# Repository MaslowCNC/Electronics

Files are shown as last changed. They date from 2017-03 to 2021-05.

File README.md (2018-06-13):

# Maslow Electronics

The printed circuit board which powers the Maslow CNC Machine

======================

Layout

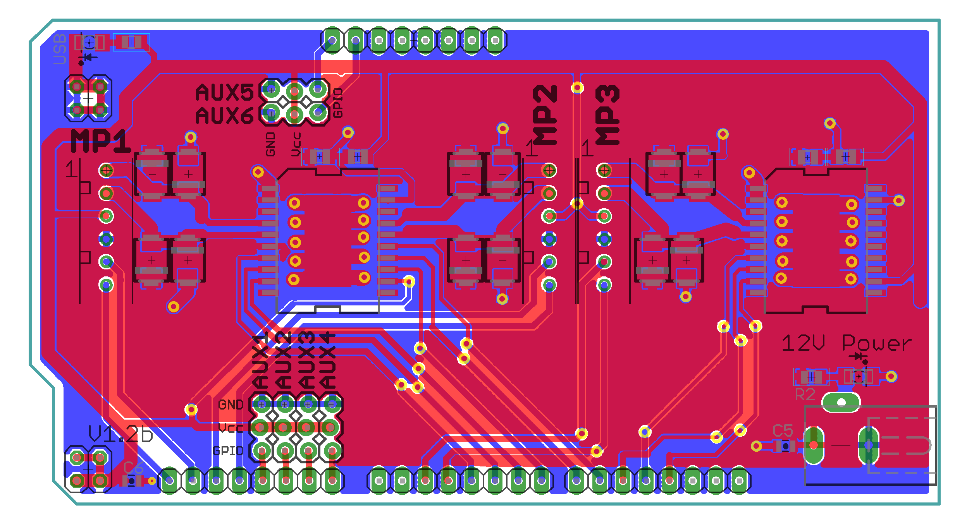
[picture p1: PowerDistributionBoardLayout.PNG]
Layout


Schematic

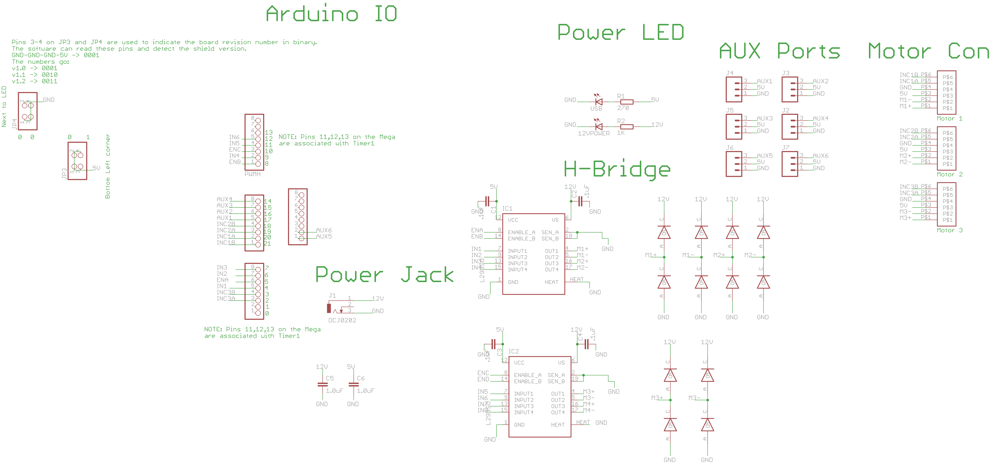
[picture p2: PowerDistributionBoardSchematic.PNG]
Schematic


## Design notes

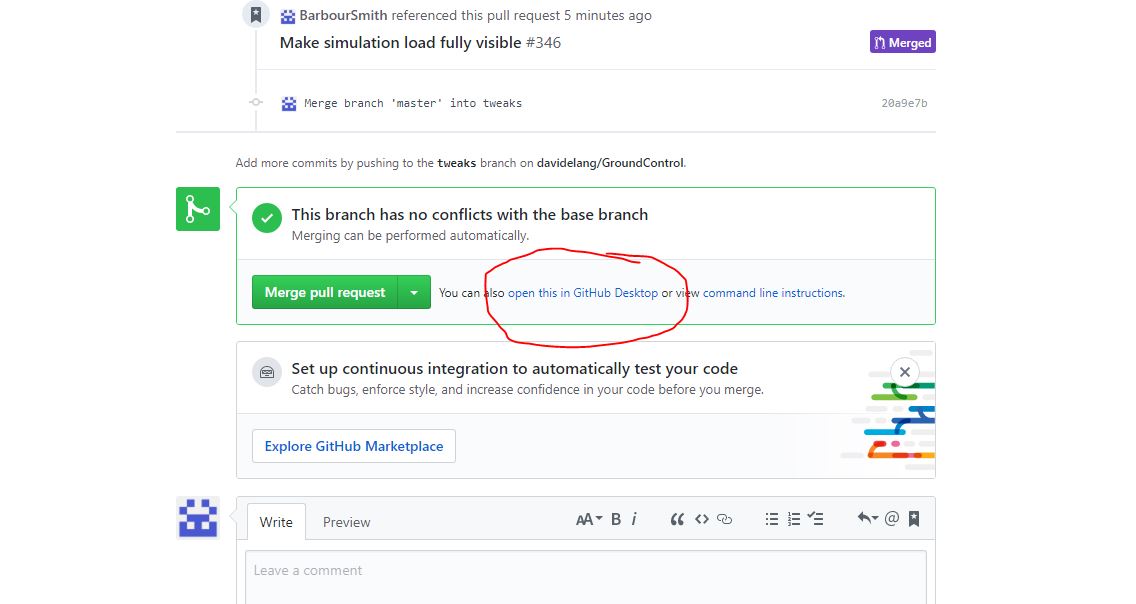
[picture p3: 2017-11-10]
Open This In GitHub Desktop.JPG

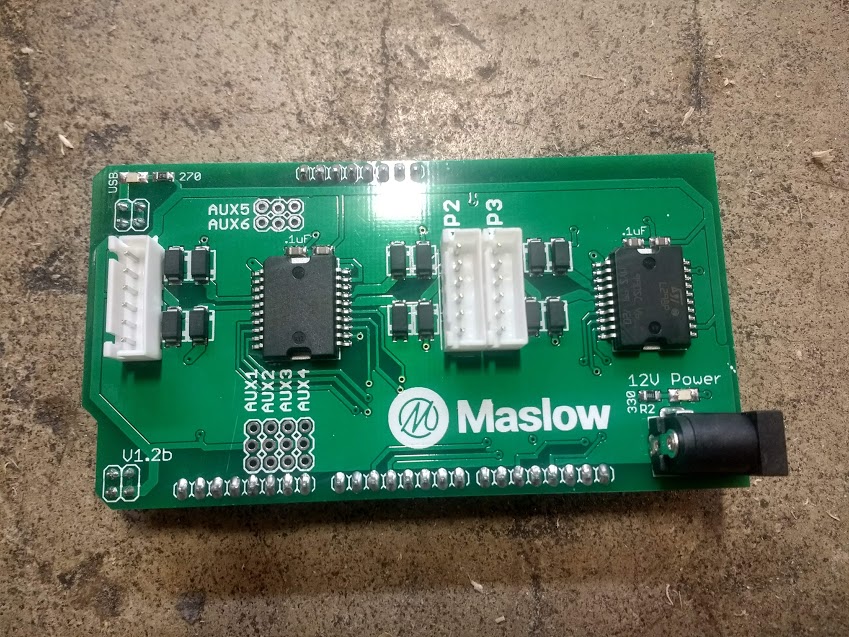
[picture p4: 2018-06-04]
mainpicture.jpg

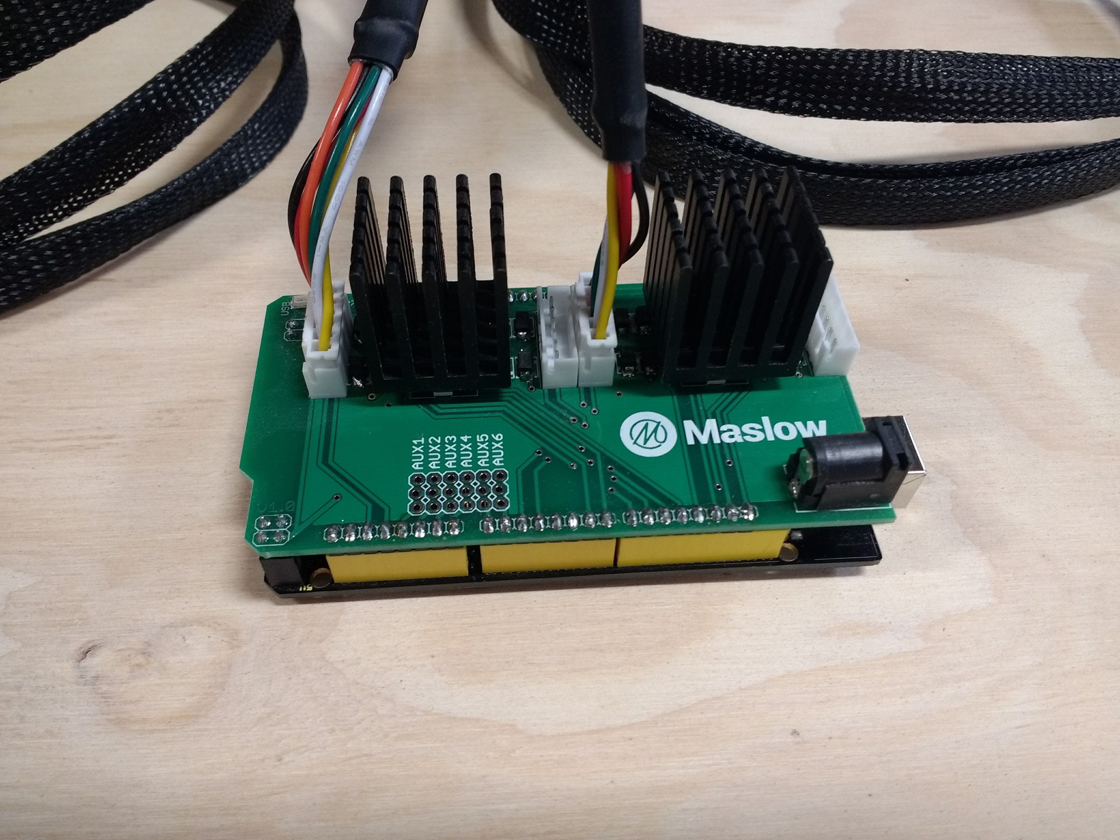
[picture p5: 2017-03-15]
Documentation/Motors Closeup.jpg

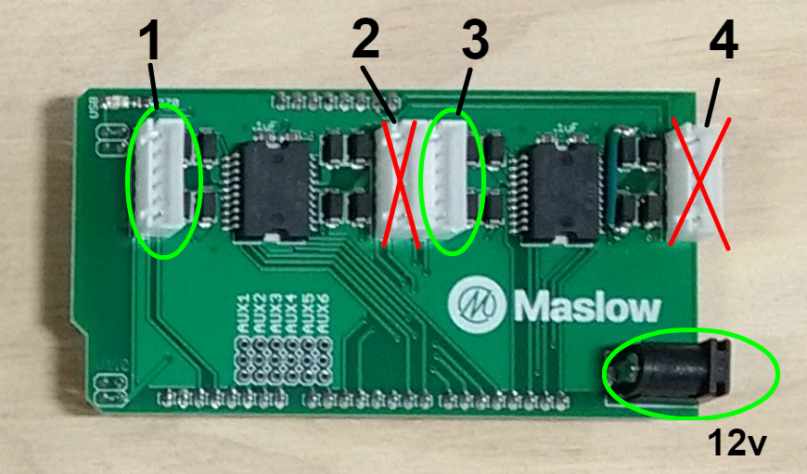
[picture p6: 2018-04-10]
Documentation/Port Closeup.png

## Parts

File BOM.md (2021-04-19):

# PCB BOM

All of the part numbers below are digikey parts unless otherwise stated.

| Part | Part # | Number Needed  | # In Schematic |
| --- |:---:|:---:|:---|
|XH-Series Connectors| 455-2271-ND | 3 | J1-3 |
| Power Jack | CP-202BH-ND | 1 | J4 |
| 1x8 .1" headers | 732-5321-ND | 4 | J5-8 |
| 2x2 .1" headers | 952-2119-ND | 2 | J9,10 |
| Flyback Diodes |  MRA4004T3GOSCT-ND  | 12 | D1-12 |
| .1uF Filter Caps | 311-1361-1-ND | 4 | C1-4 |
|  1uF Filter Caps | 445-5146-1-ND | 2 | C5,6 |
| H-Bridge | 497-3624-1-ND | 2 | IC-1,2 |
| Indicator LED | 475-1410-1-ND | 2 | LED 1-2 |
|Current Limiting R1 | RMCF0805JT270RCT-ND | 1 | R1 |
|Current Limiting R2 | 541-4162-1-ND | 1 | R2 |
| 23x23mm heatsink |Mouser-532-374124B35G| 2 | N/A |

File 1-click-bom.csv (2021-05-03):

References | Qty | Description | DigiKey | Mouser
J1-3 | 3 | XH-Series Connectors | 455-2271-ND
J4 | 1 | Power Jack | CP-202BH-ND
J5-8 | 4 | 1x8 .1" headers | 732-5321-ND
J9,10 | 2 | 2x2 .1" headers | 952-2119-ND
D1-12 | 12 | Flyback Diodes | MRA4004T3GOSCT-N
C1-4 | 4 | .1uF Filter Caps | 311-1361-1-ND
C5,6 | 2 | 1uF Filter Caps | 445-5146-1-ND
IC-1,2 | 2 | H-Bridge | 497-3624-1-ND
LED 1-2 | 2 | Indicator LED | 475-1410-1-ND
R1 | 1 | Current Limiting R1 | RMCF0805JT270RCT-ND
R2 | 1 | Current Limiting R2 | 541-4162-1-ND
N/A | 2 | 23x23mm heatsink |  | Mouser-532-374124B35G

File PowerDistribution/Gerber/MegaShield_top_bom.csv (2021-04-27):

Comment | Designator | Footprint | LCSC Part #
.1uF | 12VPOWER USB C1 C2 C3 C4 | C0805
1.0uF | C5 C6 | 0805-CAP
1K | R2 | R0805
270 | R1 | R0805
L298SO | IC1 IC2 | POWERSO-20
MRA4004 | U$2 U$3 U$4 U$5 U$6 U$7 U$8 U$9 U$10 U$11 U$13 U$14 | SMA

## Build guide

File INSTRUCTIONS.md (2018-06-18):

# Maslow Electronics Setup

We've done our best to keep the electronics for Maslow as simple as possible.

### Step 1: Identifying Parts
There are five pieces to the Maslow electronics system. Shown in the picture below from left to right and top to bottom they are:
1. The Motor/Encoder/Gear Box Units
2. Motor Wires
3. Maslow CNC motor controller shield
4. Keystudio Mega 2560 microcontroller (Arduino compatible) with USB Cable
5. 12V DC 5A / 110-250V AC Power Supply
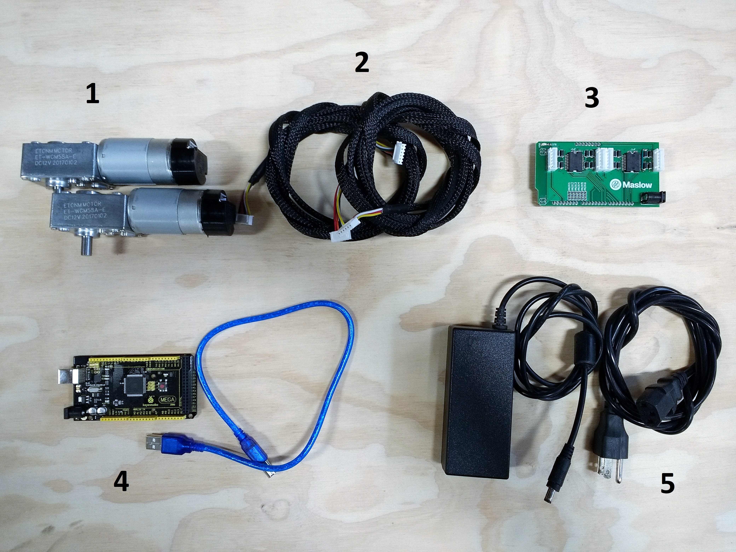
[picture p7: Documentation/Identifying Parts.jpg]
Identifying Parts


### Step 2: Attach Heatsinks
Attach the sticky backed heat sinks found in your hardware bag to the motor controller shield. (Note orientation of heatsinks)
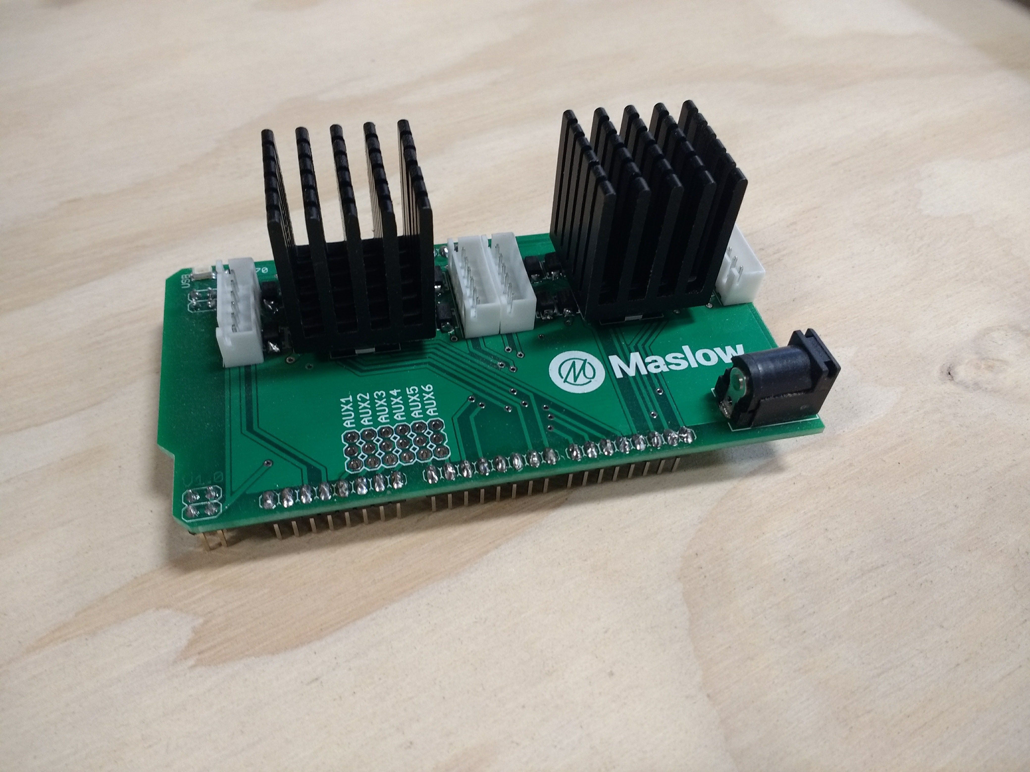
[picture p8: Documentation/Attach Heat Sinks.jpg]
Attach Heatsinks


### Step 3: Connect Arduino Shield
Attach the Arduino shield onto the Keystudio Mega 2560 microcontroller. Make sure all the pins are not twisted and that are aligned with the microcontroller before pushing the motor controller shield.
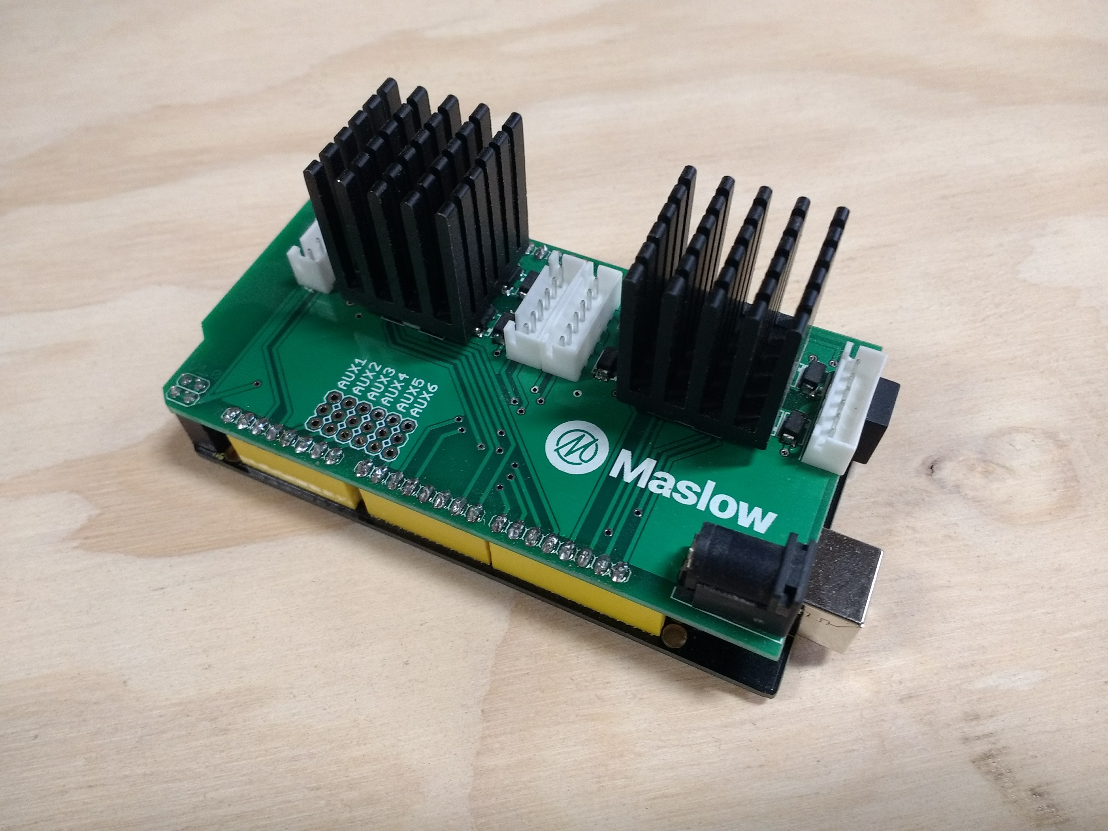
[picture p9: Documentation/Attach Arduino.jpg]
Attach Arduino


### Step 4: Connect The Motors
Attach the motors to the motor controller shield. **Note that the motors connect to ports 1 and 3 not 1 and 2**. This is to better distribute the motor power draw across both motor driver chips.  Port 3 controls the left motor and Port 1 the right motor (as viewed when facing the MaslowCNC).
The cables have two sides, so make sure that when plugged in the Arduino shield, the yellow wire is at the bottom in both ports as seen in the following photo.
When using the optional Z axis, this motor is connected to port 2.

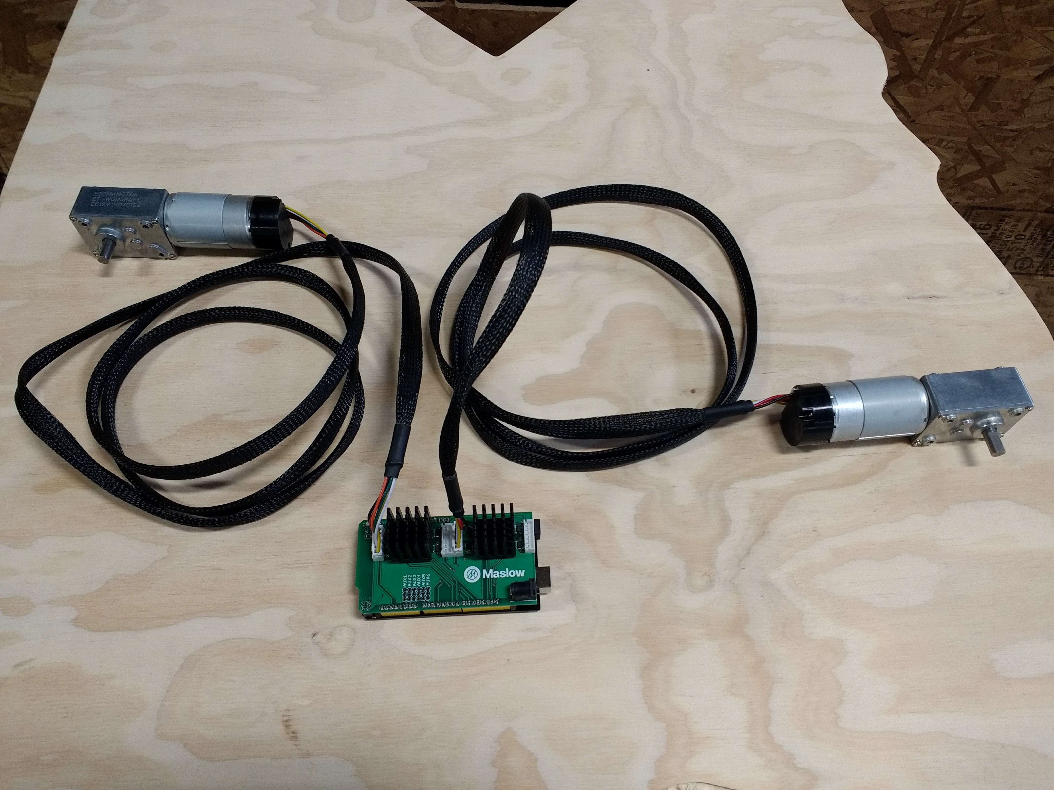
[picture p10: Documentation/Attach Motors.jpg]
Attach Motors


### Step 5: Connect The Power Supply
Plug the 12V power supply into the motor controller shield. **Note that the power supply plugs into the motor controller shield and not to the microcontroller.** Plugging the power supply into the Arduino will not damage it, but it also will not provide power to the motors. We chose the most common power supply plug to make replacements easy to find, unfortunately because it is so common this is also the same power supply plug that the Arduino uses, which is somewhat confusing.
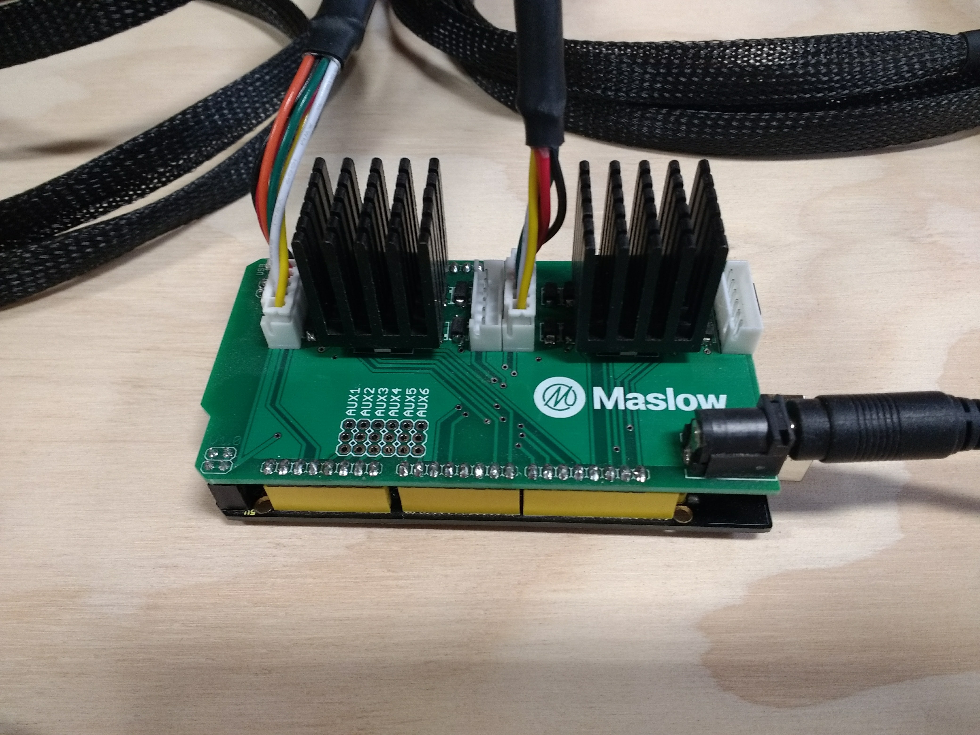
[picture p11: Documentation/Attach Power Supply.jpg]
Attach Power Supply


### Step 6: Connect The USB Cord
Plug the USB cord into the Arduino and into your computer. Note that the "USB" light will come on to indicate that the board is connected and receiving power from your computer.
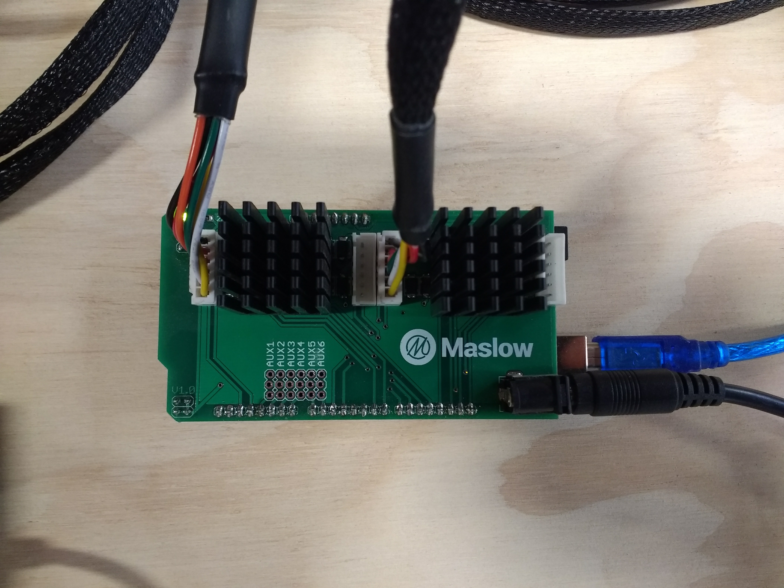
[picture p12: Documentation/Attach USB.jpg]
Attach USB


### Step 7: Proceed
You have finished setting up the Maslow electronics system. Proceed to the [next step](http://maslowcommunitygarden.org/Firmware.html?instructions=true) and install the open source Maslow Firmware on your Arduino.

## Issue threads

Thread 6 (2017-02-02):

BOM shows wrong HBridge

framecad-johnb, 2017-02-02:
The BOM currently shows a Digikey 497-1395-5-ND but the eagle file shows a surface mount component instead - I'm guessing it should be the Digikey 497-3624-1-ND, please confirm

BarbourSmith, 2017-02-03:
Thanks for catching that. I forgot to merge a pull request that fixed that. It should be up to date now.

Closed 2017-02-03.

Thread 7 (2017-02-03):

Check for continuity on 12V

blurfl, 2017-02-03:
In the area above and to the right of U$18 it looks like the top side copper pour (12V, I think) might be broken by the thru-hole of INCD1 and the keep-out around the ground pad of U$18. Is this the main 12V path to the rest of the board?
It might just be a difference in the way my tools are rendering the pours, though...
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

BarbourSmith, 2017-02-04:
That is definitely a real continuity issue. Thanks for catching that. Definitely the low point of my morning. I broke continuity there wiring up the 4th axis. I was in a huge rush to get those out because they are our longest lead time item. I am going to do a re-design next week and move all the components down so that top area is less cramped. For now I've added a wire to patch things in #8 just so the files up there aren't broken.

I checked in with the factory and its too late to do anything to the boards which are in production so I'll have to solder a wire to each of those which is pretty far from ideal. I guess this is why we do the whole beta thing.

A huge thank you again for catching that. That's a pretty big issue.

BarbourSmith, 2017-02-04:
I'd like to give you credit for having spotted the problem in next week's update. Is that OK? If so, do you have a way you would be preferred to be identified? (real name, blurfl, anonymous community member...etc)

blurfl, 2017-02-04:
I’d as soon not be identified, if that’s OK. Participation is important, glad I could help.

While I’ve got your ear, I’ve fished an old Arduino Mega 2650 out and put the firmware on it, but it seems pretty unhappy talking to GroundControl. Is it reasonable for me to try anything without the power board? Should I open a topic on the forum, or hold off until boards get to the betas?

Keep up the great work, you and Hannah are running an exciting project in an exemplary manner!

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

blurfl, 2017-02-04:
I’ve got stacks of boards with similar errors from previous projects.  A beta wouldn’t be proper without at least one “green wire”. :) The SMD Hbridges make good sense from a manufacturing angle, though. Worth the effort of the change.

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

BarbourSmith, 2017-02-04:
I'll order green wire to make the joke complete :-)

Thanks for the support. We do our best, but we really couldn't do it without you.

I wouldn't expect the lack of a power board to matter to the serial connection. What types of issues are you seeing? I tried to increase the baud rate last week and started running into issues and stepped it back so making sure you are using the current version might make a difference. I'm working on getting a Mac computer and a Raspberry Pi set up as two more test platforms in the next week. I was seeing some connection issues on the Mac which I haven't explored yet. What type of platform are you running GC on?

It might be worth filing a bug on GC for this or making a thread in the forums. I think it's something important to explore.

Closed 2017-02-05.

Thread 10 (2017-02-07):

Missing part on BOM?

pronettixs, 2017-02-07:
While reviewing the PCB in Eagle i noticed 2 component with i could not find on the BOM.
Above the H-Bridges there are 2 SMD components. Are these .1uF capasitors?

![Uploading missingParts.JPG…]()

pronettixs, 2017-02-07:
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

BarbourSmith, 2017-02-07:
Those are the .1uF filtering capacitors. I added the value to the description on the BOM to make it more clear. Thanks for pointing that out.

Do you think that's clear enough, or is there more we can do to make it clearer?

pronettixs, 2017-02-10:
Thanks, this is clear enough.

Closed 2017-02-10.

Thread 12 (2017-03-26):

Power LED should show 12V power instead of 5V

blurfl, 2017-03-26:
There presence of 5V power can be assumed if the USB connection is made; the presence of 12V power is necessary for the motors, and using this led for that would make it easy for a user to know he has the power supply correct. Relabel it '12V' or 'Motor Power'.

BarbourSmith, 2017-03-27:
Glad there is an issue for this, I agree 100%

blurfl, 2017-03-27:
It should be an easy edit, but if the boards have already been ordered…

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

BarbourSmith, 2017-03-27:
😬 It's hard to change things once the order goes out.

I've been putting off placing the next batch order to get as much feedback as possible rolled into them, but I think I need to ship them in the next few days. The basic design will be the same as in PR #9 with a 12v LED indicator added.

blurfl, 2017-03-27:
That should do it 👍

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

Closed 2017-04-11.

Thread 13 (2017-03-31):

Power supply connection

neilfrazerm, 2017-03-31:
Instructions  at setep for for those internationals without a power supply provided.
Please advise / insert the size of the connector and/or suggest supplying one in the kit if no power supply provided.
Thanks
Neil

BarbourSmith, 2017-04-01:
I checked in with Hannah and I realize this is totally my fault. I intended for those of you who live in countries with different power requirements to still receive the power supply, but just no power cord.

I chose a power supply which works from 100-250vac 50/60hz, and which uses a standard computer power cord so that they would be easy to find with the correct plug for your country.
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

I didn't make that clear enough and we ended up sending you no power supply at all. The power supply is on the way, but I understand if you don't want to wait for shipping time and want to buy one locally. I'm really sorry for the mix-up, it was completely my fault.

Fortunately, the other side of the power supply is also the most common connector I could find. Its a 5.5mm barrel connector with a 2.1mm pin. A 5.5mm barrel connector with a 2.5mm pin will also fit. The center pin is positive (standard). The supplied power-supply is a 5A  12V dc supply with self resetting fuses for over-current and over voltage protection, but almost any 12volt supply will work.

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

The power supply for the motors is isolated from the electronics so the quality of the voltage is not critical. Almost any 12 volt will work. I am more than happy to look at particular supplies if you want, and if you can find one locally that will ship more quickly than the original one which is in the mail, we are more than happy to pay for it and have it sent to you.

Again, I'm sorry for the mixup.

neilfrazerm, 2017-04-01:
Thanks awfully for sending out the supply, as you have already done so, and I am away for the next week, I shall wait for yours...

I had found the right connector from Maplins (UK Farnell equivalent) .

I do understand the pressure you are under and really do wish you rather well old chap.

Sincerest best regards,

Neil

(London)

________________________________
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

blurfl, 2018-01-10:
@BarbourSmith, this looks like it could be closed, but your reply and its pictures look like good wiki fodder 😀

Closed 2018-01-10.

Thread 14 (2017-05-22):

Motor Control Pins - are two GPIO pins necessary?

blurfl, 2017-05-22:
It looks like the two motor control pins are always used in complementary states in Motor.cpp. Could each motor be controlled by one GPIO and an inverter to use fewer GPIO pins?

BarbourSmith, 2017-05-23:
No, we could really use just one pin and an inverter.

Using two pins keeps the part count down (we've already got the pins).

In theory we could do active braking of the motor by using both pins high (or maybe it's low), but I haven't played with that option yet.

blurfl, 2017-05-23:
Using one pin eases the task of adapting other cpu options (ESP32). The inverters could live on the adapter board instead of on the motor board.
With the present gearing setup, would adaptive braking accomplish much?

Closed 2017-05-23.

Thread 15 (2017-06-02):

PWMH Connector

1996Donzi, 2017-06-02:
Per the eagle file the connector labeled PWMH has two pins (IN7 and IN8) if I am looking at the Arduino Mega  schematic properly they are tied to GND and AREF, is this correct?

BarbourSmith, 2017-06-02:
You are correct, that was a mistake. The latest PCB version (updated this morning) removes that connector.

Closed 2017-06-06.

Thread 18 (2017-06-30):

Missing Heatsink from BOM

JDogHerman, 2017-06-30:
In the pictures I see a heatsink shown but it is not an item on the electronics BOM. Can this be added?

BarbourSmith, 2017-06-30:
Great point! Yes it can

BarbourSmith, 2017-06-30:
I've added it to the BOM. Its good that it is in there to remind people to order one when buying parts. I can't give you a digikey number for the part because we had ours custom made, but it's not a critical part. Digikey sells a number in the right size range.

JDogHerman, 2017-06-30:
Will there be a method of purchasing these "one off custom" parts from the MaslowCNC org?

JDogHerman, 2017-06-30:
What sort of thermal resistance is required?

JDogHerman, 2017-06-30:
Would a part like Digikey: 345-1103-ND work? Its a "little" larger but it already has the adhesive base.

BarbourSmith, 2017-07-01:
That one looks perfect. I measured the space and it will fit. I would recommend the taller 25AB model because the short one might not move enough heat.

If you want to throw it in the BOM that would be fantastic.

We're probably never going to sell the heatsinks individually because it's not really cost effective, but we will probably sell the whole arduino shield as a board with the heat sinks in the next few weeks

JDogHerman, 2017-07-01:
Added the suggested heatsink to pull request #19

schlaubi0666, 2017-07-12:
the sugested one is also 6.4mm in heigth, but the one on the Picture is much taller ...
is this ok , to use the not so tall Version?
or better use ATS1319-ND ?

JDogHerman, 2017-07-12:
@schlaubi0666 It looks like the ATS1319-ND does not have numbers for thermal resistance while being naturally cooled.  Its also more than 3 times the price. (might be necessary) @BarbourSmith does this part @schlaubi0666 suggested look like a more fitting part?

JDogHerman, 2017-07-12:
The nice thing is since the H-Bridge is over-temped protected and it is a closed loop system, if the H-Bridge does go into over-temp the encoder will detect that it has missed steps and the cut wont be lost.

In a future board design it might be nice to use L298N as it has much better thermal transfer numbers vs the L298P. 3C/W vs 13C/W*while using a aluminum substrate (not used in current boards)

BarbourSmith, 2017-07-12:
While they say it's over temp protected, we've blown up enough at this point to put that in the false marketing category ☹️

I think I tracked down a part that I was looking at as a replacement in the future, but I can't remember what it is off the top of my head. Moving away from the L298 family is in the future.

blurfl, 2018-01-10:
@BarbourSmith, have you got a heatsink (and thermal tape) part number for the BOM?

Also your comment "Moving away from the L298 family is in the future." [Issue #23](https://github.com/MaslowCNC/Electronics/issues/23) is a discussion about this general topic - any further thoughts?

BarbourSmith, 2018-01-10:
We ended up having them custom made 🙄 so I don't have a part number. It's weird how it's cheaper to have a heatsink made to spec than to buy one off the shelf

I hadn't given too much thought to moving away from the L298 family because we stopped blowing them up with such regularity...I still think moving is a good idea...I am a little worried about possible effects to the PID tuning

blurfl, 2018-01-10:
I think I've ordered replacements for these.I think I've got Digikey part numbersfor the [thermal tape](https://www.digikey.com/product-detail/en/3m-tc/15MM-15MM-10-8810/3M10310-ND/2649855) and the heat sinks, but I haven't found the heat sink one yet 🙃. I'll keep looking and reply to this issue.

blurfl, 2018-01-10:
I was wrong, the heat sinks were for a different chip family, not applicable. Are there enough on hand to offer them in the Maslow store?

blurfl, 2018-01-12:
[This](https://www.mouser.com/productdetail/aavid-thermalloy/374124b00035g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) heatsink from Mouser is 23mm x 23mm and 18mm high, so slightly shorter but in the ballpark. In stock, $2.35 each, includes the thermal tape.

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

BarbourSmith, 2018-01-12:
That looks like a perfect solution!

blurfl, 2018-01-12:
Shall I add it to the BOM in the same PR that updates the schematic and silkscreen, or would you like them separated?

BarbourSmith, 2018-01-12:
Having a lot of pull requests that change the board files themselves can be tricky, but doing this as a separate PR should be safe I think

blurfl, 2018-01-12:
Oops, I'll pull the PR back and separate them - sorry, jumped the gun!

blurfl, 2018-01-12:
While I'm at it, should I be saving these files in a particular version of EAGLE v8.5 is current, but it offers an option to save for EAGLE v7.x ?
Also, I'd like to remove the backup files and lock file that EAGLE leaves around - only the .sch and .brd files in the repo.

blurfl, 2018-01-12:
@BarbourSmith, here's the situation - The pin label changes affect the schematic visibly and the board invisibly, so both must be changed together. The silkscreen change affects the board but not the schematic, but both files should still be submitted together.
 I did the schematic change first as it made a bigger change. Shall I remove the diode symbols from the board file that goes with the schematic change, open a PR for just the schematic change, then add the diode symbols to the silkscreen after the schematic PR is merged?

BarbourSmith, 2018-01-12:
Right, I see the issue

Is it possible to submit just both changes at once? I think that would be totally OK

blurfl, 2018-01-13:
This was addressed in PR#41 - is it Ok to close this?

BarbourSmith, 2018-01-13:
I vote to close this one as well. You are really knocking these off!

Closed 2018-01-13.

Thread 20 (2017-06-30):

Heatsink substrate

JDogHerman, 2017-06-30:
I might be wrong in this, but would it be good to add a thermal substrate copper pad for the H-Bridge ICs to sit upon?

BarbourSmith, 2017-07-01:
I think it's a great idea. We actually had one in an early version of the PCB, but I took it out because our PCBA people were having enough trouble and I wanted to make things really really really easy for them. It might be time to put that back in. The ground plane runs right under each chip to make doing exactly that easy.

JDogHerman, 2017-07-01:
Sorry I opened this and then looked closer at the traces and saw that the traces run underneath the ICs.

dmouw25, 2017-09-01:
Is it possible to Reopen this?   These packages are designed to dissipate most of the heat through slug on the bottom of the package.  If you notice, the datasheet does not give thermal values for junction to case.   You would likely get better thermal performance with a redesigned PCB and no heatsink.

JDogHerman, 2017-09-01:
Reopened as a feature request.

blurfl, 2018-01-10:
I believe this was addressed in the v1.2 layout. @JDogHerman, @dmouw25 does that look correct to you? If so, we could close this.

BarbourSmith, 2018-01-10:
I second that it was a great suggestion and has been added

Closed 2018-01-10.

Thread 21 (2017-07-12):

how to get a pcb

schlaubi666, 2017-07-12:
i missed Kickstarter, and you do not know it you are selling kits again ;-(

1. do you will provide an partlist soon ?

the most difficult part to get is the pcb of the Driver ....

2. you have some spare modules to sell ?

3. it not, can you provide the gerber data to order my own pcb ?
4. what is the spec/Parameter of your ordered pcb's ?

br

Dirk

BarbourSmith, 2017-07-12:
We're hoping to start selling individual parts really soon, so hopefully in a couple weeks you will be able to buy an arduino shield from us in the next few weeks.

Until then, we do have a parts list here: https://github.com/MaslowCNC/Electronics/blob/master/BOM.txt and the gerber files are available here: https://github.com/MaslowCNC/Electronics/tree/master/PowerDistribution if you want to make your own.

The specs for the boards are nothing special. Maybe 16mil trace width and 1oz copper. Anyone who can make PCBs should be able to make one for you.

JDogHerman, 2017-07-14:
@schlaubi0666 I am in the same boat with you. I put in an order for a PCB and got more than I needed (min quantity). PM me if you would like me to get you one at cost+shipping.

schlaubi0666, 2017-07-15:
the part list  a was taking about , is the whole list , not just the electronics ...

schlaubi0666, 2017-07-15:
@JDogHerman : i did not found an way th contact you (PM) , so yes i would like to have on. plz. write me an email to my username + @gmx.de

JDogHerman, 2017-07-17:
@schlaubi0666 I got an email bounceback from the gmx.de server. Is there another address I can contact you at?

ndefoor, 2017-07-18:
@JDogHerman Could you message me  nathandefoor@hotmail.com I would like to see about getting one of those extra boards. Thanks

mgood83, 2017-07-20:
@JDogHerman could you also message me in regards to purchasing a board from you. I was just about to get one made, but if you already have spare, even better. Happy to pay send payment for cost + time +shipping. Thanks. mwgoodlett@gmail.com

clintloggins, 2017-07-20:
@JDogHerman please count me in if you have another pcb. More than happy to pay a premium!! Also, any of the changes that you discussed I am willing to test and give feedback. Thanks!
clintloggins@gmail.com

schlaubi666, 2017-07-20:
thanks for selling the bord now in your shop , i will grab one there ....

ndefoor, 2017-07-26:
I am looking for the specifics on the motors.  Does it matter if the rpms are slightly different?

JDogHerman, 2017-07-26:
@ndefoor There is a discussion on alternative motors options on the forums.

[forum link](http://forums.maslowcnc.com/t/for-those-that-were-not-part-of-the-kickstarter-where-to-obtain-the-main-motor-worm-gear-encoder/120)

JDogHerman, 2017-07-26:
This issue can be closed.

Closed 2017-07-26.

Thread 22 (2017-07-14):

Silkscreen is missing LED polarity

JDogHerman, 2017-07-14:
It might be nice to see the LED polarity shown on the silkscreen for those of us that are sadistic enough to build our own boards.

Also why not show a website address? maslow.cnc 👍

BarbourSmith, 2017-07-17:
Those are both great suggestions

blurfl, 2018-01-10:
I'm going to be into the design files working on the schematic for [issue #36(https://github.com/MaslowCNC/Electronics/issues/36). I'll open a separate PR to add this and update the board .jpg as well.

blurfl, 2018-01-11:
Rather than draw an LED symbol, I've put a plus sign opposite the positive end of each of the two LEDs:
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

If that's satisfactory, I'll put in a PR with the change.

BarbourSmith, 2018-01-11:
I think that looks great!

BarbourSmith, 2018-01-11:
There is a small dot on the LED part, does that not indicate polarity?

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

BarbourSmith, 2018-01-11:
My read of the schematic is that the polarity should be like this:

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

blurfl, 2018-01-11:
Thanks Bar, you're right. Hard to turn my thinking around to 12V power plane and routed ground. The dot _does_ indicate polarity, but I think it wouldn't appear on the silkscreen of a PCB in a maker's hand because it's in a keep-out area. The plus would address that. You've got a good point, though - SMD LED's use a dot to mark the cathode end. How best to address the issue, dot-at-cathode or plus-at-anode? @JDogHerman, what's your opinion?

BarbourSmith, 2018-01-11:
I think the plus is a great idea! I was just pointing out the dot because I was curious what it meant. You are absolutely right that it does not show up anywhere on the PCB. I actually had an email from the manufacturer this morning to confirm the diode directions so even they are confused 😛

The plus will be much better.

blurfl, 2018-01-11:
Just to stir the pot, how about:
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

and
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

BarbourSmith, 2018-01-11:
SLICK! I love it

blurfl, 2018-01-13:
This was addressed in PR#42 - is it Ok to close this?

BarbourSmith, 2018-01-13:
Also beautifully taken care of. I vote to close.

Closed 2018-01-14.

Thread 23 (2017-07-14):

New board design discussion.

JDogHerman, 2017-07-14:
Since this shield has lots of room on it what if there was thru-hole passive components holes added to the board in addition to smb. That way the board could be built as a kit easier for mortals.

BarbourSmith, 2017-07-17:
It might seem like there is a lot of space, but a lot of the open copper is actually left intentionally open because we have a lot of current flowing across the board. I'm open to the idea if someone can design one that looks good, but I think we'd be better off doing a second board that's the through hole version if we want that

JDogHerman, 2017-07-17:
If the XH connector housing was moved down it would allow for more room for the A+ B+ motor lines to be widened and permit though hole diodes to be added. (in addition to reducing the trace length)

The current limiting resistor and LEDs have plenty of board room and the filter caps could be moved closer to the supply rather than near the H-Bridges. #27

In addition if the MP3 H-Bridge was moved to the right it would help provide less thermal coupling with the other H-Bridge.

BarbourSmith, 2017-07-17:
Those are great points! If you make those changes, I'd be more than happy to merge them. My only reservation is that I think I'm going to redesign with a new H-bridge chip so we're probably going to see a lot of changes soon

JDogHerman, 2017-07-17:
@BarbourSmith what H-bridge chip are you thinking? Maybe I can help propose a layout with the new chip in mind.

BarbourSmith, 2017-07-17:
That would be great! I'm thinking about using the L6206 (https://www.digikey.com/product-detail/en/stmicroelectronics/L6206PD013TR/497-3643-1-ND/677626)

JDogHerman, 2017-07-17:
Interesting. The L6206 has integrated diodes, and higher current capacities, but if thermal considerations havn't been built into the PCB. The heat will skyrocket with 62 C/W! 🔥

BarbourSmith, 2017-07-17:
Good spot, that's something we need to consider. 62C/W is nuts, how does anyone keep that cool?

JDogHerman, 2017-07-17:
Looks like you can get it down to 15C/W by having it

> Mounted on a multilayer FR4 PCB with a dissipating copper surface on the top side of 6 cm2 (with a thickness of 35 µm),
> 16 via holes and a ground layer.

then maybe adding heatsinks and active cooling could keep it cool. ❄️

Also did you see that digikey has limited numbers of this pn?

BarbourSmith, 2017-07-17:
I (clearly) didn't do too much research into finding a replacement part yet, and I'm rapidly becoming convinced that the L6206 is not the best choice. Are there any other candidates out there that look more promising?

JDogHerman, 2017-07-17:
What features are you hoping to achieve?
More current? Higher voltage? Better thermal characteristics? Faster switching?

BarbourSmith, 2017-07-17:
I'd say the #1 thing we need is durability. I'd like a chip that we can short without blowing it up, and which doesn't overheat easily. Other than that our needs are for a pretty basic 12v 2A+ H-Bridge

JDogHerman, 2017-07-18:
Have you seen this? [TLE5206-2GCT-ND](https://www.digikey.com/products/en?keywords=TLE5206-2GCT-ND)

Low Thermal Resistance, Internal Inductive Diodes, Short circuit protection with a error pin so software could alert the user that there was an issue. Cost is higher but isnt bad.

Better pcb thermal design features and a heat sink would still be necessary but the chip should have better reliability since it will have more headroom vs the existing [chip 497-3624-1-ND](https://www.digikey.com/product-detail/en/stmicroelectronics/L298P013TR/497-3624-1-ND/677613)

BarbourSmith, 2017-07-18:
Crikey, I love it! Excellent find! The price is pretty reasonable even with one needed per motor. The board will still be a couple $ more, but for full output short circuit protection it's absolutely worth it.

I'll see if I can throw together a board to test them this weekend, when I have PCBs made, I'd be more than happy to send you some to test too if you'd be interested.

blurfl, 2017-07-18:
I’d like to test or help with the design too, if I might.
When laying it out, here are some things to think about:

- Could we re-think which pins are used for board ID? The present approach interferes with the ICSP pins, making porting to other processors harder and making it harder to use SPI. Too, using a pull-up/down resistor adds parts count, but protects the gpio pins.
- As we don’t need the braking function, the new layout could use hardware inverters to handle the complement motor drive signals.
- It would be harder to deal with heat sinks, but putting the motor drivers on daughter boards or using the thru-hole version of these chips would make it easier for mortals to repair. Selling motor drive daughterboards as spares would mean less electronic waste when the drivers need replacement.

JDogHerman, 2017-07-18:
@BarbourSmith that sounds great. If you want help with ideas on the design of the PCB let me know. I would be thrilled to test or help design. Just let me know how I can help. We could even add this as a project to github.

@blurfl I too would think a new method for identifying board revisions might be nice.  In fact if there was interest in changing the H-Bridge communication path to SPI there are other chip that could fill that need.

blurfl, 2017-07-18:
Having SPI available would make it possible to add SD card support.

- gcode transfer serial buffering is an ongoing issue. With a local file system we could transfer separately from the cutting process and the read from there while cutting instead.
- This could make off-line operation possible as well.
- Finally, some other processor boards have higher speed, but don’t have the non-volatile storage of the Mega. An SD card would open up those possibilities as well.

 So, while I build my wish list, let me add at least the traces for a micro SD card :)

BarbourSmith, 2017-07-19:
Any and all help is more than welcome, if you want to have a go at putting together a board with the TLE206 or any other chip that you think is worth a go I would love to try it out!

I agree that adding an SPI interface could be nice. My general preference is to keep the whole machine as simple and low cost as possible to keep it reliable and affordable, but that doesn't mean we couldn't have the pins broken out to attach an SD card daughter board. Going to SPI for the motor controllers is also an option. I used the simplest most reliable interface for the boards so far because I wanted to focus on getting as simple and robust a system as possible built, but now that we have a stable platform to work from, there's no reason not to try new things.

JDogHerman, 2017-07-19:
Here is an SPI H-Bridge I was also looking at. https://www.digikey.com/product-detail/en/infineon-technologies/TLE6209RAUMA2/TLE6209RCT-ND/2231220

blurfl, 2017-07-19:
That’a an interesting chip - bigger and more expensive, but it makes the detailed failure info available.

Have you seen anything that could take the burden of interfacing with the motor encoders? That’s presently handled using interrupts on the Mega, and the code for that is inline assembly in order to keep up. I think it might be limiting how fast we can travel. Surely something else could watch the encoder pulses and provide direction and step count when queried. I’ve seen this [LSI-LS7184](http://anaheimautomation.com/manuals/ics/L010546%20-%20LSI-LS7183,%20LSI-LS7184.pdf), but they aren’t widely available.

blurfl, 2017-07-19:
I see there is an SPI version, LS7366, that includes the counter as well, but only available from the manufacturer :(

blurfl, 2017-07-22:
@JDogHerman, it doesn't look like the  TLE5206 will do speed control. Am I missing something? I'm disappointed, I like the TO220 thru-hole option.

mrfugu, 2017-08-15:
If you're considering a significant re-design of the Shield board, please consider adding the necessary provisions to allow installation of a cheap (iOS compatible) [Bluetooth Module](https://www.itead.cc/serial-port-ble-module-master-slave-hm-10.html) .

dmouw25, 2017-08-29:
Is there any description / datasheet for the motors used?  I can't find it in the wiki.  Thinking about starting a redesign of the board with better heatsinking of the ICs, and better diodes, but want more details on the motors before I start the design phase.  Board would be optimized for automated assembly, not hand assembly.

blurfl, 2017-08-29:
A description from the [wiki](https://github.com/MaslowCNC/Mechanics/wiki/DIY-Kit-Mechanical-Equivalent-Parts):
Motor/Gearbox/Encoder	(291:1 reduction gearbox with worm gear to prevent back driving motor, 30kg/cm torque, 20 rpm, 12 volts)

Some discussion on the forum, [here.](http://forums.maslowcnc.com/t/for-those-that-were-not-part-of-the-kickstarter-where-to-obtain-the-main-motor-worm-gear-encoder/120/35)

mrfugu, 2017-08-29:
@dmouw25 In tinkering with the shield, attempting to get a bluetooth module integrated, I'll note that it would be very useful if all the unused pins, but most especially the digital pins, passed (unmolested) through the shield and were able to be accessed from 'above'.

JDogHerman, 2017-09-10:
I created a branch design using the TLE5206-2G not sure how people feel about it but here it is.
https://github.com/jdogherman/electronics/tree/TLE5206-2G-Board

blurfl, 2017-09-10:
This looks good! I wonder if a few more vias non the M1-, M2- and M3- lines would be advisable. Not much current capacity in a via! Alternately, make those larger to allow a wire thru-soldered.

JDogHerman, 2017-09-10:
@blurfl good point! I have updated the design with 4 vias per leg.

blurfl, 2017-09-11:
I'm not seeing the 4-via version in your repository yet?
Are all the signals the same, only the H-bridges changed?

JDogHerman, 2017-09-11:
wow somehow I missed adding the new file. It's there now. The signals are all the same but the 12v lines have more vias.

blurfl, 2017-09-11:
I hate to say, but the commit show 0 changes in 0 changed files. GitHub is a fickle mistress...

JDogHerman, 2017-09-11:
Sorry been under the weather and I must not be thinking too clearly. I see the changes on https://github.com/JDogHerman/Electronics/commit/d9fb86bcf717d573a443468bce3ea259ec66f5bf Can you check that you can see the changes?

blurfl, 2017-10-19:
@JDogHerman,  I've been looking at the TLE5205 and TLE5206 again lately. Have you looked at the firmware changes to drive these?

blurfl, 2018-01-29:
I have a working board using the TLE5206. It requires changes to System.cpp and Motor.cpp for new pins and a different method of controlling the chip,

blurfl, 2018-06-01:
With the release of the TLE5206 board in the Community Garden, most of the ideas have been implemented with the exception of the connection for a Bluetooth module.
 Would it make sense to close this?

Closed 2018-06-01.

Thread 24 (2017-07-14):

Motor shield image is from older board design

JDogHerman, 2017-07-14:
The shield image shown in the documentation shows a board with 4 motor hookups not 3 like in commit 5ab7ff7

This may want to be changed so others might not seem confused.

BarbourSmith, 2017-07-17:
Great suggestion, I've updated them in #26

Closed 2017-07-17.

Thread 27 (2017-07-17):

Capacitor location & are C3 & C4 needed?

JDogHerman, 2017-07-17:
I'm looking at the board and I was wondering if C3 & C4 were really necessary. Since C1 & C3 (5v filter) are in parallel and C2 & c4 (12v filter) are the same, would it not make sense to just use a larger capacitor and move those caps away from the warmer H-Bridge and towards the supply?

This would allow better heat dissipation to the H-Bridge along with reducing the part count.

BarbourSmith, 2017-07-17:
That's a great point. We could probably get away with just one set of filtering capacitors, especially since the only parts pulling from that 5v rail are the two H-bridges and an LED which won't add spikes

dmouw25, 2017-08-27:
I would highly recommend leaving both Capacitors in place.  Actually the C1 & C3 should be moved closer to the IC to prevent power glitches from causing odd behavior.    Adding a bulk capacitor to the VDD_12V would probably be a good idea as well since the motors are drawing significant amounts of current.  Application diagram in datasheet for the motor driver had a 470uF electrolytic.

Package size on the ceramic capacitors could be reduced from 0805 to 0603 to make layout easier, but 0805 is better for ESD (ESD can damage 0603 capacitors, but 0805 can generally absorb the energy without damage).  If this was my design I would place an ESD rated 0805 capacitor at the power connector and 0402 at the ICs for local decoupling.

blurfl, 2017-08-29:
I agree, leave the caps. They are recommended by the chip manufacturer.

Closed 2017-08-29.

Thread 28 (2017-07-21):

Aux vias are not in a grid.

JDogHerman, 2017-07-21:
The 5v pin on Aux vias 1-5 are not inline with the ground pin. The silk screen is good but the pin is off. I can see this on the board I had printed and from the board in the store.

BarbourSmith, 2017-07-22:
Yes! (but this is intentional 😀 )

If you stick headers in them they will be held in place by the slight offset making it easier to solder

blurfl, 2017-08-29:
Is the explanation sufficient? Can this be closed?

Closed 2017-08-29.

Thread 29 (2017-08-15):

Feature Request: iOS Compatible Bluetooth

mrfugu, 2017-08-15:
Hey,

As an adjunct to issue #23. I have located an iOS compatible BLE 4.0 compatible board:

https://www.itead.cc/serial-port-ble-module-master-slave-hm-10.html

Multiple Ebay sellers have them for less than $2.50 per piece. It kinda seems like a no brainer to add to any major redesign of the shield. The price differences of adding BLE on the Audrino side is many  times (>10x) this cost.

Beyond the obvious benefits of the average iOS device (computing power, ease of use, install base) as it relates to running GC, having any GC host with a reliable wireless connection + (eventual) spindle control would, in my opinion, add a considerable safety factor to the machine that needs to be considered. (in the context of the ongoing spindle control discussion)

Thinking beyond the firmware, take [a look at the ARKit](https://developer.apple.com/videos/play/wwdc2017/602/) and consider how MaslowCNC/GC could pretty relatively easily gain Computer Vision, and incorporate camera based safety and accuracy protocols.

blurfl, 2017-08-15:
Note that the first comment on the product page talks about having bought one of those from eBay and gotten a “knockoff with limited functionality with firmware“.
[This](https://www.adafruit.com/product/2479) unit, while more expensive, is readily available and well supported.

blurfl, 2017-08-15:
As the BLE module uses the same Tx and Rx lines as the normal USB serial connection, a provision to select between the two - pin jumper or switch - might be useful/necessary.

blurfl, 2017-08-15:
As a BLE connection is less reliable than a wired serial one, it might be a good idea to link this enhancement to an enhancement for adding stand-alone operation with the gcode stored on-board the Maslow.
Transferring a gcode file and monitoring the machine status seems reasonable to expect from a BLE connection.

mrfugu, 2017-08-15:
I've just committed to purchasing a 'test rig', maslow shield + audrino + BLE module i linked above.  I'll report results as soon as I have em and can get em talking.  with my goal of getting an iOS build of GC up and running via BLE.

Wish me luck!

BarbourSmith, 2017-08-15:
Good luck!

blurfl, 2017-08-15:
Best of luck!

mrfugu, 2017-08-20:
Update:

I've got my testing rig partially together and am continuing research. I have a MaslowShield, KeyeStudio Mega board, and for Bluetooth I selected a MakerFocus DX-BT16 Bluetooth module. They're cheap, seemingly plentiful, should work fine via BLE

Cables and a breadboard are still a day or 2 away from arrival, and I'm continuing my research on the MacOS/iOS side of things.

This appears to be the [best candidate](https://github.com/adafruit/Adafruit_Python_BluefruitLE) as it can keep as much as possible within python. It doesn't specify iOS compatibility, but CoreBluetooth (Apple's BLE Framework) should hold over between MacOS and iOS,

When building for iOS it appears that python libraries are all packaged into the iOS app (via https://github.com/kivy/kivy-ios) so I'm hoping for a little luck and that this won't be super complex to achieve.

More as I have it.

blurfl, 2017-08-20:
I think in OS X you’ll be able to talk to the Bluetooth serial port  without any other drivers, once it’s been paired. The groundcontrol app should offer to connect to that serial port in its menu available ports.

mrfugu, 2017-08-20:
that's clearly the case with pre-BLE devices as they used the Serial Port Protocol standard (which btw, is unavailable to iOS), but I'm not sure it is the case with BLE (>4.0 devices). iOS needs explicit UUID definitions that may or may not be (i simply don't know) automatically identified by MacOS.

mrfugu, 2017-08-24:
Update: I have all the hardware finally and have started by writing an include for the firmware, "ble.h", to configure the BLE module (and add other BLE chipsets easily).

It then mirrors the USB 'Serial' port and hopefully not be a problem for GC.

I figure that I'll add a toggle/selector for enabling the BLE module in GC once I get there, but for now I want to make the Arduino respond on either USB or BLE. I should have it all cleaned up and integrated into a Firmware-BLE branch tomorrow.

Moving on to new MacOS and iOS forks of GroundControl:

I can currently see the BLE module using BLE sniffer apps on both MacOS and iOS, but I cannot see them in the SystemPrefs/Settings apps. This might be a MFi (made for mac/ios) licensing thing, and the app will have to manage that stuff, I dunno yet.

For MacOS, I have successfully installed pyobjc and can see a big long list of apple's CoreFrameworks (inc CoreBluetooth) in pip (/usr/local/bin/pip). I hope to have an initial BLE enabled MacOS build of GC next week sometime.

For iOS, the Kivy-ios packager wants its own python that it inserts into the iOS app and I haven't figured out how to add packages to kivy-ios's python build yet. Kivy-ios needs to build for various architectures from there, so it's a showstopper if I can't get pyobjc (and the apple CoreFrameworks) into the kivy-ios python. If I can, and it works (there's no documentation I've found that says so either way at this point) we're probably good to go.

blurfl, 2017-08-24:
GCwants to see data received from the firmware every 200ms or so, or it decides it has lost the link.
On the Mega, will you be using the same rx/tx lines that the USB serial connection uses?

mrfugu, 2017-08-24:
yeah, timing and Baud rates were a question that I was going to wrestle with shortly.  Currently GC sets the Serial speed to 57600, iOS and Android want 115200.. I figured some timing issues might pop up if i force the firmware to the faster rate.

As for the pins I'm using, I can use 0 and 1, but i think its a better idea to use other pins, I have them currently on pins Maslow would use as I'm just making sure I have the variables and strings all correct to easily re-configure and reset the bluetooth module. I was going to move them to an unused set, i was thinking 50 and  51. so I didn't use up anything already in use.

It's not optimal that the firmware currently uses all 3 aux Serial pins for the motor controllers, but from what I see its not a big deal right now. I have read though that it's possible to send multiple control signals via a single pair of pins. Perhaps that's worth looking into for the next shield revision, It'd be good imho to free up those serial pins.

Back to the link-connection-timeout stuff, I'm sure it'd be possible for the firmware to kick out data at a rate that maintains the BLE link, or instruct GC to expect how the BLE link prefers to behave.  I think it's telling that GC drops the link often enough with a wired connection, those issues should be solved independently of adding BLE. But i'm not a 'real' dev so I don't really know for sure. =)

blurfl, 2017-08-24:
I think the 200ms timeout is arbitrary, but it could be confusing if it was kicking in.

dmouw25, 2017-08-27:
Before you get too far, I would recommend testing how reliable the bluetooth connection is when a router is running.  DC motors produce a lot of broadband RF noise and the bluetooth connection may or may not work.

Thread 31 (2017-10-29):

J4 - Power Jack Part Number

blurfl, 2017-10-29:
Is it possible that the part used for J4, the 12V power jack changed from the device shown in the BOM?
The BOM shows a CP-002A-ND, which has a 2mm center pin. The jack on the v1.1 board has a 2.5mm center pin. The DigiKey part number for that would be CP-002B-ND.

BarbourSmith, 2017-10-30:
Great catch @blurfl

I checked the invoice and the part we are using is [CP-202BH-ND](https://www.digikey.com/product-detail/en/cui-inc/PJ-202BH/CP-202BH-ND/408451 )

I will update the BOM right now

blurfl, 2017-10-31:
I see, that one has the higher (5A) current rating. From a company from Tualatin, OR., too 😄

BarbourSmith, 2017-10-31:
No way! That's a 15 minute drive away and I had no idea. Maybe we'll drop by to say hello

Closed 2018-01-10.

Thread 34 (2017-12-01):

Add Temp Probes or Jumpers for Temp Probes

krkeegan, 2017-12-01:
Given some issues with burning up the bridges, a temperature probe on each one, even an external probe stuck in the heatsink might be helpful.  The Firmware could pause or slow down if in an over temp state.

blurfl, 2017-12-06:
AUX 5&6 are analog inputs as well as gpios, so no need for a board change 😉. A daughter board with the circuitry for the temp sensor and to switch power for the fan could use one AUX for the temp sensor and the other for the fan control. A 2x3 connector on AUX5&6 would take power, ground and the signals to/from the daughter board. Power for the fan could come from the 12V supply or a separate supply. Using the 12V supply would take some thinking, though...

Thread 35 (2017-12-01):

Add a Fan or Jumpers for a Fan

krkeegan, 2017-12-01:
I know we are limited on amperage but a small fan would be great.  The fan could tie into the temp probes I proposed in #34 to speed up and down as needed.  Or in a simple scenario just turn on when the firmware is active.

blurfl, 2017-12-06:
"just turn on when the firmware is active." That could be as simple as a 'startup block' like grbl implements to execute at startup. gcode M106 sets fan speed, M105 reads 3D printer bed temperature - these could be used with the daughterboard I suggested in #34

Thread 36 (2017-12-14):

Electronics Schematic Labelling does not match software pin mapping

insoleaf, 2017-12-14:
The Electronics Schematic for the Maslow CNC Motor Shield has different Arduino Pin Mapping Labels from the latest revision of the software for V1.2 of the PCB which is the closest match.

The inconsistencies are as follow and should be looked at for completeness
The discrepancies are as follows

1. Software mapping PCB Revision 1.2

Software shows AUX ports are AUX1 = 17, AUX2 = 16, AUX 3=15, AUX4=14
Electronics Schematic shows AUX1=14, AUX 2=15, AUX3=16, AUX4 = 17
I am not sure if the schematic is correct or the software pin mapping as I am not sure anyone uses these but this should be looked into

2. Software mapping PCB Revision 1.2

Software Mapping Encoder1A=20, Encoder1B=21, Encoder2A=19, Encoder2B=18 , Encoder3A=2, Encoder3B=3
Electronics Schematic shows Encoder1A=18, Encoder1B=19, Encoder2A=21, Encoder2B=20 , Encoder3A=3, Encoder3B=2

Given that the system is working for other users the software mapping must be correct and the electronics schematic  incorrect. This should be looked into

blurfl, 2018-01-10:
The schematic has been different from the silkscreen and software since the beta days. I'll open a PR to change the v1.2 schematic and replace the .jpg of the schematic. Do we want signal, ground and Vcc indicators nest to the rows of pins as well (or should that be a separate PR)?

BarbourSmith, 2018-01-10:
I think one PR would be OK. Doing version control on the PCB files is so dicey anyway that I vote less pull requests is better to avoid conflicts

insoleaf, 2018-01-11:
Thanks for your Reply Scott,
The Schematic in its current form is perfect the pin mapping just need to
match the current version of the software and hardware revision as noted.
The reason I requested the change is that I am documenting the Maslow
Building Blocks so that others trying to understand the code can make a
connection with the hardware. It would also be helpful to indicate which
revision number of the hardware the schematic represents and putting in the
Signal Ground and Vcc indicators next to the row of pins is a great idea. I
think we can do all of that in the one PR

Currently the Wiki shows Software pin mappings up to version 1.2 of the
Motor Shield hardware.

On Thu, Jan 11, 2018 at 4:50 AM, Scott Smith <notifications@github.com>
wrote:

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

--

stuartnicole.richards@gmail.com

blurfl, 2018-01-11:
Here is a modified schematic with the nets renamed to match the silkscreen and the firmware. Note that I've moved J2, J3, J4 and J5 around to keep the AUX pin names in order as well:
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

and the companion board layout with labels for the AUX GND and Vcc:
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

insoleaf, 2018-01-11:
Scott,
I have checked the schematic and there is still an issue with the mappings
for The Encoder Channels A & B.

If you look at System.cpp and check the mappings for version 1.2 of the
hardware board the mappings should be as follows

else if(pcbVersion == 2){
//PCB v1.2 Detected
//MP1 - Right Motor
ENCODER1A = 20; // INPUT
ENCODER1B = 21; // INPUT
IN1 = 4; // OUTPUT
IN2 = 6; // OUTPUT
ENA = 5; // PWM
//MP2 - Z-axis
ENCODER2A = 19; // INPUT
ENCODER2B = 18; // INPUT
IN3 = 7; // OUTPUT
IN4 = 9; // OUTPUT
ENB = 8; // PWM
//MP3 - Left Motor
ENCODER3A = 2; // INPUT
ENCODER3B = 3; // INPUT
IN5 = 11; // OUTPUT
IN6 = 12; // OUTPUT
ENC = 10; // PWM
}

Kind Regards Stuart

On Thu, Jan 11, 2018 at 3:22 PM, Scott Smith <notifications@github.com>
wrote:

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

--

stuartnicole.richards@gmail.com

blurfl, 2018-01-11:
You're certainly right, the encoder signal names for motors 1 & 2 were wrong. I've re-done the IN__ names for Motors 1&2.
Thanks for catching this too. Here's the result:
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

insoleaf, 2018-01-11:
Scott,
Almost there. The pin mapping for Encoder 3A and 3B need to be swapped as
3A is pin 2 and 3B is pin 3.

I was also looking at the data sheet for the H-Bridge and note that the Ena
is on Pin 6 and Enb on Pin 11 as per the diagram below.

The schematic has Ena on pin 5 of the Arduino which is connected into the
H-Bridge Driver on Enable_A however it is labelled with Pin 8 so this does
not look correct. Also Enb is on pin 8 of the arduino which is then
connected into the H-Bridge Driver on Enable_B however it is labelled  Pin
14 so this does not look correct either.

From the Firmware
Arduino Pin 5 (ENA) is actually connected to pin 6 of the H-Bridge Driver
Chip
Arduino Pin 8 (ENB) is actually connected to pin 11 of the H-Bridge Driver
Chip

Unless I am missing something the pin mappings on the H-Bridge Driver
Schematic don't look correct
[image: Inline image 1]

Kind Regards Stuart

On Thu, Jan 11, 2018 at 5:41 PM, Scott Smith <notifications@github.com>
wrote:

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

--

stuartnicole.richards@gmail.com

blurfl, 2018-01-11:
I've swapped INC3A/INC3B on the schematic.
 The diagram you mention didn't make it into the comment, but it sounds like you're quoting pin numbers for the 'Multiwatt15' package L298N or L298HN; we're using the 'PowerSO20' package, L298P.
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

Is that the issue?

blurfl, 2018-01-11:
Here's the schematic that addresses INC3A/INC3B:
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

insoleaf, 2018-01-12:
Apologies Scott you are 100% correct. The pinouts in the Schematic were for
the Multiwatt 15 and not the PowerSO20.

Thanks for making those amendments.

Kind Regards Stuart

On Fri, Jan 12, 2018 at 5:55 AM, Scott Smith <notifications@github.com>
wrote:

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

--

stuartnicole.richards@gmail.com

blurfl, 2018-01-12:
That's Ok, thanks for going into the files in such depth. Is the Schematic ready for a PR, then?

insoleaf, 2018-01-12:
Yes Scott the Schematic is ready for PR.

Kind Regards Stuart

On Fri, Jan 12, 2018 at 11:04 AM, Scott Smith <notifications@github.com>
wrote:

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

--

stuartnicole.richards@gmail.com

blurfl, 2018-01-13:
This was addressed in PR#42 - is it Ok to close this?

BarbourSmith, 2018-01-13:
Yes, I believe so. Well taken care of 👍 👍 💯

Closed 2018-01-13.

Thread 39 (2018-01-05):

Add ability to drive stepper

davidelang, 2018-01-05:
see https://github.com/MaslowCNC/Firmware/issues/355

since we are have four channels available, it would be good to add an extra header to the board that would let us use two channels together to drive a stepper (ideally using the same pinout that is common for 3d printers)

combined with a software way to drive this (even inefficiently), this would let people use off-the-shelf stepper driven Z axis kits/design with the maslow.

blurfl, 2018-01-10:
This would involve a fairly major re-design of the board.

BarbourSmith, 2018-01-10:
Yes, it would probably be easier to make a new board. I am going to add the tag wontfix because the suggestion is a good one, but we are not actively working towards addressing it

davidelang, 2018-01-10:
On Wed, 10 Jan 2018, Scott Smith wrote:

> This would involve a fairly major re-design of the board.

I don't think it would.

a stepper driver is two H bridges, one for each set of coils. The pre-built
steppers add extra logic to simplify management of the two h-bridges so that you
can have one pin for direction and another for step and the chip takes care of
everything else.

But if we just were to wire the two H-bridge halves to one plug, the rest of the
logic could be done in software.

It's not efficient, and not pretty, but I can't think of why it wouldn't work.

Remember, we are not needing microstepping here, the stepper (@200 steps/rev) is
being connected to a lead screw (@8 steps/in or more), resulting in one step
being ~ 0.00125". That should be more than sufficient for the Z axis. I'd expect
that we could get by with a resulution 1/10 that (0.0125") without a problem.

So a simple state table in software that we step through to toggle the different
combinations of power through the h-bridges should be easy to do.

Doing something to drive these at less than full power (pwm) shoudn't be that
hard either.

blurfl, 2018-01-10:
I'd call it a major re-design as it involves adding another connector and traces for the connector and the presently unused half of the second H-bridge. Further, the present design has spread the chips out for thermal efficiency, leaving no room for a fourth connector.

blurfl, 2018-01-10:
If one wants to drive a stepper, look into driving a stepper driver board using two of the AUX pins. Logic power, ground, step and direction are enough for the Maslow side and are all available from the AUX pins.

BarbourSmith, 2018-01-10:
Great suggestion @blurfl I think driving a stepper off of the AUX ports makes so much more sense and would be a much cleaner build. Ok to close this as a hardware issue and make it a software issue if we decide to go that route?

ProtoMakerOpenTech, 2018-09-10:
Currently working on a maslow variant for the open source market. Going to work on keeping it as backward compatible as possible and will be building a new board for stepper control, support for a lathe axis and VFD. Anyone interested in contributing let me know. Most of my machine design experience is in the 3D printing space and came across the maslow as a possible tool for prototyping.

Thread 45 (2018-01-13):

LED Current too high

dmouw25, 2018-01-13:
The current through the 12VPOWER LED is too high and power dissipation of R2 is very high.   LED is rated for 25mA maximum and LED is currently being driven at 29mA ((12V-2.2V)/330 ohm).   Resistor R2 is currently dissipating 290mW typical.  Increasing resistor R2 to 1000 ohm would allow a normal 0805 resistor to be used instead of thick metal film resistor selected for a small cost savings and will reduced board power dissipation by 190mW.   This will set LED to a  nominal current of 10mA and worst case current at ~12mA.   This will match the 5V LED current,   If maximum brightness is desired, R2 can be set to 510 ohm, which should guarentee that LED current stays below 25mA (assuming 12V supply stays under 13V)

blurfl, 2018-01-13:
A good catch! Great that you're checking deeply into the circuitry. Do you want to do a PR on this, or shall I?

dmouw25, 2018-01-13:
Not sure how to do a PR, so could you do it?

blurfl, 2018-01-13:
I'll be glad to. To summarize, I'll change the value of R2 to 1K on the schematic and the BOM, and look up a 1K SMD thin-film resistor for the BOM, yes?

dmouw25, 2018-01-13:
Correct.   I would personally go with 541-4162-1-ND at digikey But that is mostly because that is a company we use at work.

blurfl, 2018-01-13:
I'm a great fan of DigiKey too. Thanks for the part number 💯

BarbourSmith, 2018-01-13:
Excellent suggestion! Let's change the part in the BOM and change the value for that resistor in the schematic. 👍 👍 💯

blurfl, 2018-01-18:
Ok to close this?

BarbourSmith, 2018-01-18:
I vote to close. Well added!

Closed 2018-01-18.

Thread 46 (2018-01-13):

Catch Diodes are not fast recovery diodes

dmouw25, 2018-01-13:
The 4004 diode is a general purpose diode and is not designed as a fast recovery diode.  Datasheet for motor driver recommends "The external bridge of diodes D1 to D4 is made by four fast recovery elements (trr ≤ 200 nsec)".   A quick search of digikey found the ES1JFSCT-ND which has a reverse recovery of 35nS vs the 4004 which is not specified.  I suspect we should really go with a schottky diode such as the SSA210 (digikey SSA210CT-ND), but my expertise is  more in DC/DC power supplies and design for automotive EMC.   I will ask around at work of a couple of graybeards and see if they have any advice on an appropriate diode for this application

BarbourSmith, 2018-01-13:
Excellent point! Let's change this.

blurfl, 2018-01-13:
Let's wait to hear what the 'graybeards' have to say. When we hear back, we'll "make it so" 😁

dmouw25, 2018-01-17:
So I talked with the guys at work and going to the schottky is a good idea but with one caveat that requires testing.  That said I am not convinced it is worth the cost unless it actually helps performance.

Caveat:
Schottky diodes are known for their high temp current leakage.  For the diode specified, it has  typical leakage at 125C and 10V of 250uA.  (room temp 100nA)  The datasheet specifies a absolute maximum of 20mA @ -100v and 100C, but realistically you probably never see more then 1mA. The biggest concern would be that the leakage would cause the motor to move.  I don't think that would happen with 1mA of current, but don't know.  This could be tested by powering the motor through a 12k resistor to 12V and see if any movement occurs.

Really what should be done is try it on one board and see if power dissipation in the motor driver decreases and if the ~0.40 is worth it or not.

The bigger issue is that the Motor driver IC has a absolute maximum rating of 3A vs the stall current of the motor being 14.6A (according to datasheet in github).  There is a fairly large voltage drop across the H-bridge since it is bipolar based design, so the actual stall current is likely lower, but still is  going to exceed the part ratings by a large amount turning the motor driver into a very expensive silicon fuse.  Fixing the diodes or adding better heatsinking isn't going to fix that issue.

I design automotive electronics for a living, so I tend overdesign everything since returns from the field are very expensive.  If you are not getting large fallout in the field, it may not be worth changing anything.

If you are still getting parts failing, The real way to improve the reliability is to go to a motor driver that has built in current limit, but that would involve a complete redesign to a new IC family.

blurfl, 2018-01-18:
The failures we've had were the H-bridge portions of the driver chips in the stall situation. It doesn't sound like the Schottky diodes would address this.
 I wonder whether the faster recovery diodes would make any noticeable difference in performance - our switching rate is 490 Hz at present.
 I've built a board using a different driver (TLE5206) which looks promising, but it uses a subtly different approach to control, and I haven't had the time to write a patch to drive it yet. I've got spare unpopulated boards if you're interested.

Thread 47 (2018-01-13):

Not enough Capacitance on 12V rail

dmouw25, 2018-01-13:
I should start this issue with a comment that I do not have a Maslow, so this is all theoretical.

The 12V supply is a standard brick and i am assuming it is a 36" cable between power supply and Maslow PCB.   Signal travel along PCB or wires at ~ 6" per ns.  This means when additional current is required from power supply, it takes 12nS for power supply to respond (6 nanoseconds to get to power supply, then 6 nanosecond to get back).

The basic capacitor equation is I=C DV/DT.   Assuming a stall current of 2amp , capacitance of 0.2uF and time of 12nS.  Rearranging to solve for Voltage, DV = I*DT/C and inputting values, we get DV =2*12nS/0.2uF.   DV = 120mV.

Personally I think 120mV of ringing on the 12V line is unacceptable and would recommend adding  1uF capacitor to 12V reducing the ringing to 20mV.   This noise may be coupled into the encoder or USB traces causing issues with those signals.

I would also add a 1uF to the 5V line, but that is more paranoia based on best practice.    I would recommend the 445-5146-1-ND from digikey and add to both 12V line and 5V line.  You can get 1uF capacitors in 0603 package, but we have found at work that 0603 can sometimes be damage by ESD strikes, so 0805 or greater should be used.  The .1uF capacitors could be reduced to 0402, but understand that some people find that hard to solder.  A 4.7uF or greater electrolytic capacitor could also be used, but it takes up more board space and is more expensive.

blurfl, 2018-01-13:
If I understand correctly, one should be able to see a ringing on the 12V plane in sync (at the same frequency as) with the PWM signal driving one of the motors at a moderately high load. One could look for that same frequency on the 5V line and encoder lines to check for crosstalk.
 To date we haven't had a lot of issues that seemed cross-talk related, but conservative engineering is not a bad idea. It wouldn't be hard to add a couple caps to the design - near the point where the 12V and 5V line come onto the board, yes?

dmouw25, 2018-01-13:
That seems correct.  The ringing will repeat at the same rate as PWM, but the frequency of the ringing will be dependant on actual length of 12V harness.   It may also be prudent to add pads for a large electrolytic near 12V input, but skip by default.  a 6mm x 6mm such as Digikey part # 493-2190-1-ND would be perfect.

BarbourSmith, 2018-01-13:
I think adding 1uF capacitors to both the 12v and 5v lines is a good idea. @blurfl is right that we haven't seen much in the way of issues here, but capacitors are cheap and adding them is easy. 👍 👍

blurfl, 2018-01-14:
I'm going to hold the PR for this back until PR #48 is merged; this uses the schematic and board files from that branch. Don;t know how else to do this, trying to avoid a conflict.

BarbourSmith, 2018-01-15:
Smart!

blurfl, 2018-01-18:
Ok to close this?

BarbourSmith, 2018-01-18:
I vote to close

Closed 2018-01-18.

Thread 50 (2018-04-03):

Add a fuse

matmaxgeds, 2018-04-03:
It would be great to explore a fuse to prevent the motor drivers burning out when e.g. the chain wraps and the sprockets get stuck as suggested here: https://forums.maslowcnc.com/t/a-jam-burnt-the-motor-driver-board/3106/24

matmaxgeds, 2018-04-03:
If we made up some with the connectors, that would also be a good retrofit option for those who already have boards - bonus points if it is resettable

blurfl, 2018-04-03:
It will probably require s PCB for the male connector - it's only available as a [board-mounted device](https://www.digikey.com/product-detail/en/jst-sales-america-inc/B6B-XH-A(LF)(SN)/455-2271-ND/1000381)

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

The [mating connector](https://www.digikey.com/product-detail/en/jst-sales-america-inc/XHP-6/455-2218-ND/1651016)
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

and [pre-crimped pins](https://www.digikey.com/product-detail/en/jst-sales-america-inc/ASXHSXH22K305/455-3241-ND/6684932) for that connector
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

The board would make a good place for the fuse holder, though.

baverhey, 2018-07-20:
I was planning to add a fuse what would be the amperage needed and response time/curve?

BarbourSmith, 2018-07-20:
I can't give you an exact correct answer, but my instinct says something that would blow after about 250ms at 3 amps is probably a good starting point. Feedback on if that is a good number would be awesome.

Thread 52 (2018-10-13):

Heat sinks do not stick to motor controller chips

elfa45, 2018-10-13:
Am putting the electronics together.  I am unable to make the heat sinks stick to the motor controller shield chips.
I removed the backing and applied to the chips.  They stick for awhile but any movement of the board might cause them to fall off.  The tape still feels sticky but does not hold.

Is there another option for applying the heat shields?

jbarchuk, 2018-10-13:
Wipe the chips with alcohol. They may not have been cleaned properly.
Trying several times and falling off, the tape on yours is deteriorated
some. If it doesn't stick, thermal epoxy is best.

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

darigovresearch, 2021-04-17:
@elfa45 did this help resolve your issue?

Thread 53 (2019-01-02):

I need a z axis cable

Darkir1, 2019-01-02:
I don't have a z axis cable and I need to get one. what is the contact email?

BarbourSmith, 2019-01-03:
Unfortunately October 2018 was the last time that I had spare parts. I recommend contacting [MakerMadeCNC](https://forums.maslowcnc.com/u/makermadecnc/summary) through the forums to see if they can set you up with one. I'm sorry I can't send you one myself!

Darkir1, 2019-01-05:
I am currently putting together the cable I  need from online stock suppliers. I can start assembling packages for cables only anyone wants to buy one.

BarbourSmith, 2019-01-05:
I think that would be fantastic. Hopefully nobody else is missing one, but it could be useful for those who are assembling their own kits from parts. Listing the cable in [The Market](http://maslowcommunitygarden.org/?market=true) could be a good way to let people know it is available.

darigovresearch, 2021-04-17:
@Darkir1 Have you managed to solve this issue for yourself or put up a listing on the market?

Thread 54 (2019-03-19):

Need a new Arduino shield

medic2410p, 2019-03-19:
I am needing a new shield. Anyone know where I can buy just the shield?

darigovresearch, 2021-04-17:
@medic2410p you can try [the market](http://maslowcommunitygarden.org/?market=true) we're also trying to make it easier to order the PCB and parts with Kitspace (see issue #57) if you're electrically inclined.

Did you manage to resolve this issue since it was posted?

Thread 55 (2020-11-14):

I got a micro usb cord....its supposed to be a printer style cord end?

ezgo123, 2020-11-14:
I ordered the maslow kit and im trying to connect everything only to find out i recieved a usb to micro usb cord...that doesnt connect to the board. I need a usb to printer style connector.

BarbourSmith, 2020-11-14:
That's wild. Who did you order the kit from?

ezgo123, 2020-11-14:
I ordered it through Amazon

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

GeroBH, 2020-11-15:
The Arduino DUE uses micro usb. Check your order if it was for an Arduino MEGA, then the cable is wrong. If your order was for the Arduino DUE you got the right cable but the wrong microcontroler.

BarbourSmith, 2020-11-15:
Ahhh @GeroBH  is correct. That sounds like the right USB cable. It could also be that you are following the wrong instructions. MakerMade CNC sells the kit you got so it might be worth checking to see if they have different assembly instructions

GeroBH, 2020-11-15:
MakerMade still sells a kit with the Mega and a newer kit with the Due, so the question is what kit did you order.
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

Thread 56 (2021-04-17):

[BUG] Dead link to store for PCB board

darigovresearch, 2021-04-17:
Page in question - https://github.com/MaslowCNC/Electronics/blob/master/BOM.md

BarbourSmith, 2021-04-19:
Thanks for pointing that out, I took the link out

Closed 2021-04-19.

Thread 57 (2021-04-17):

[FEATURE REQUEST] Add Kitspace one click pricing

darigovresearch, 2021-04-17:
[Kitspace](https://kitspace.org/) is a project that really helps with building open source hardware as it allows you to (when properly implemented) have an almost one click pricing for the PCB and electronics components. If setup by the maintainers it would really decrease uncertainty if the components chosen are the ones that work reliably.

We haven't had to implement it yet but it seems relatively straightforward to implement and lets users have self-autonomy to replicate the work, build upon it and put it in the hands of users.

Examples of very good implementations of this are the [Open book](https://kitspace.org/boards/github.com/joeycastillo/the-open-book/open-book/) and [ebook wing](https://kitspace.org/boards/github.com/joeycastillo/the-open-book/ebook-wing/) projects by @joeycastillo

https://kitspace.org/1-click-bom/
https://github.com/kitspace/1clickBOM#readme

BarbourSmith, 2021-04-19:
I fully support this. Does the kit designer get a cut of the profits from the orders? If so I am absolutely OK with you putting it up there and keeping any money made from it.

darigovresearch, 2021-04-24:
@BarbourSmith I believe the cost only covers the price of the PCB and components but am sure a support button or profit sharing feature may be implementable. @kasbah could you please advise?

I am working on a pull request to add the project to kitspace but it requires gerbers to be exported so #59 needs to be resolved before it can be completed

kasbah, 2021-04-24:
Kitspace doesn't currently take any money except for the few kits I put together personally that are on shop.kitspace.org. The other orders all go directly to 3rd parties. The PCB companies listed are sponsors through [our Opencollective](https://opencollective.com/kitspace).

darigovresearch, 2021-05-01:
Have added a pull request #62 that would resolve the issue. @BarbourSmith I believe this must be merged before @kasbah can add the project to the kitspace website

BarbourSmith, 2021-05-03:
Great! Let's make it happen. Thanks for the pull request 👍

Closed 2021-05-03.

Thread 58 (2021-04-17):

[FEATURE REQUEST] Add Kitspace one click pricing

darigovresearch, 2021-04-17:
[Kitspace](https://kitspace.org/) is a project that really helps with building open source hardware as it allows you to (when properly implemented) have an almost one click pricing for the PCB and electronics components. If setup by the maintainers it would really decrease uncertainty if the components chosen are the ones that work reliably.

We haven't had to implement it yet but it seems relatively straightforward to implement and lets users have self-autonomy to replicate the work, build upon it and put it in the hands of users.

Examples of very good implementations of this are the [Open book](https://kitspace.org/boards/github.com/joeycastillo/the-open-book/open-book/) and [ebook wing](https://kitspace.org/boards/github.com/joeycastillo/the-open-book/ebook-wing/) projects by @joeycastillo

https://kitspace.org/1-click-bom/
https://github.com/kitspace/1clickBOM#readme

darigovresearch, 2021-04-17:
This is an accidental duplication of #57 from clicking submit twice most likely

Closed 2021-04-17.

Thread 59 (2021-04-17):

[FEATURE REQUEST] Export Gerber files

darigovresearch, 2021-04-17:
Kitspace requires a folder of Gerbers so that they can be easily ordered from the various PCB suppliers they are linked to in order to get a price. It would also help for people who just want to order boards but don't have access to EAGLE

Could you export the Gerbers into a folder called `Gerbers` in the `PowerDistribution` folder?

We would do it but we don't have access to EAGLE

This would help with respect to issue #57 if you think it is worth us making a pull request

darigovresearch, 2021-04-17:
@kasbah can you confirm that Gerbers are required for Kitspace and the one click BOM to work?

kasbah, 2021-04-17:
At the moment, yes. We have been meaning to implement auto-plotting of Gerbers for Eagle for ages now. It's implemented for KiCad but not for Eagle.

BarbourSmith, 2021-04-19:
Unfortunately I also don't have access to Eagle anymore. Once Autodesk bought it it won't run on my computer anymore 😞

darigovresearch, 2021-04-24:
@BarbourSmith no worries, maybe someone from the community has access to it and could oblige. @kasbah or @midopple do you have access to Eagle to just make a pull request with exported gerbers in a suitable folder in [Power Distribution folder](https://github.com/MaslowCNC/Electronics/tree/master/PowerDistribution)?

May be worth trying to port the Eagle file into [KiCad](https://www.kicad.org/) to avoid the eagle issue for other users in the community

midopple, 2021-04-26:
Hi,

I have exported the Gerberfiles, see the Pull #61

darigovresearch, 2021-05-01:
@midopple thanks for resolving this issue!

Closed 2021-05-01.

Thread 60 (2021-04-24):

[FEATURE REQUEST] KiCad version of PCB

darigovresearch, 2021-04-24:
We may get more contributions/improvements to the system if it is in an open source PCB format like KiCad as it would reduce the barrier to entry for new users. Was wondering if the maintainers or someone from the community would be interested in trying this out.

https://www.kicad.org/

darigovresearch, 2021-04-24:
@midopple any chance you could do what you done to resolve https://github.com/drspangle/infidel-sensor/issues/24 here?

midopple, 2021-04-26:
Hi,
i have added the Kicad Files #61
Please check it, at my first check i see no errors

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

darigovresearch, 2021-05-01:
Hi, @midopple thanks for being kind enough to tackle this issue. We're still learning KiCad but will raise any issues if we see any pop up so will close this as you managed to generate the files which is a great start!

Closed 2021-05-01.

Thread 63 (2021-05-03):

[BUG] Missing outline on the .mil file for the Gerbers

darigovresearch, 2021-05-03:
See https://github.com/MaslowCNC/Electronics/pull/62#issuecomment-830635273 for more details

Jamtek, 2021-08-01:
I noticed two large rectangular shapes outside the board outline.
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

Removed the outside rectangles and regenerated the Gerber and drill files in KiCad. They now appear in the TraceSpace view portal as well as OSH Park.
![2021-08-01_18-31](https://user-images.githubusercontent.com/35613772/127787284-127eb73a-71bf-4d7b-9e
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
af-e5285739b7ce.png)

BarbourSmith, 2021-08-02:
I think those rectangles are the copper pours which create the ground plane and the power plane so they should be there.

Jamtek, 2021-08-04:
Ok, rookie mistake on my part. So maybe the actual issue was that the copper pours did not surround the entire board. Red Top pour is not surrounding the entire board outline. When I enlarged it to encompass the entire board and hit shortcut B to fill all zones, I was able to generate the Gerber files Edge_Cuts or board outline.
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

BarbourSmith, 2021-08-04:
I vaguely remember there being a reason for it not going all the way to the edge, but I can't remember what it would be. Is it OK to close this issue?

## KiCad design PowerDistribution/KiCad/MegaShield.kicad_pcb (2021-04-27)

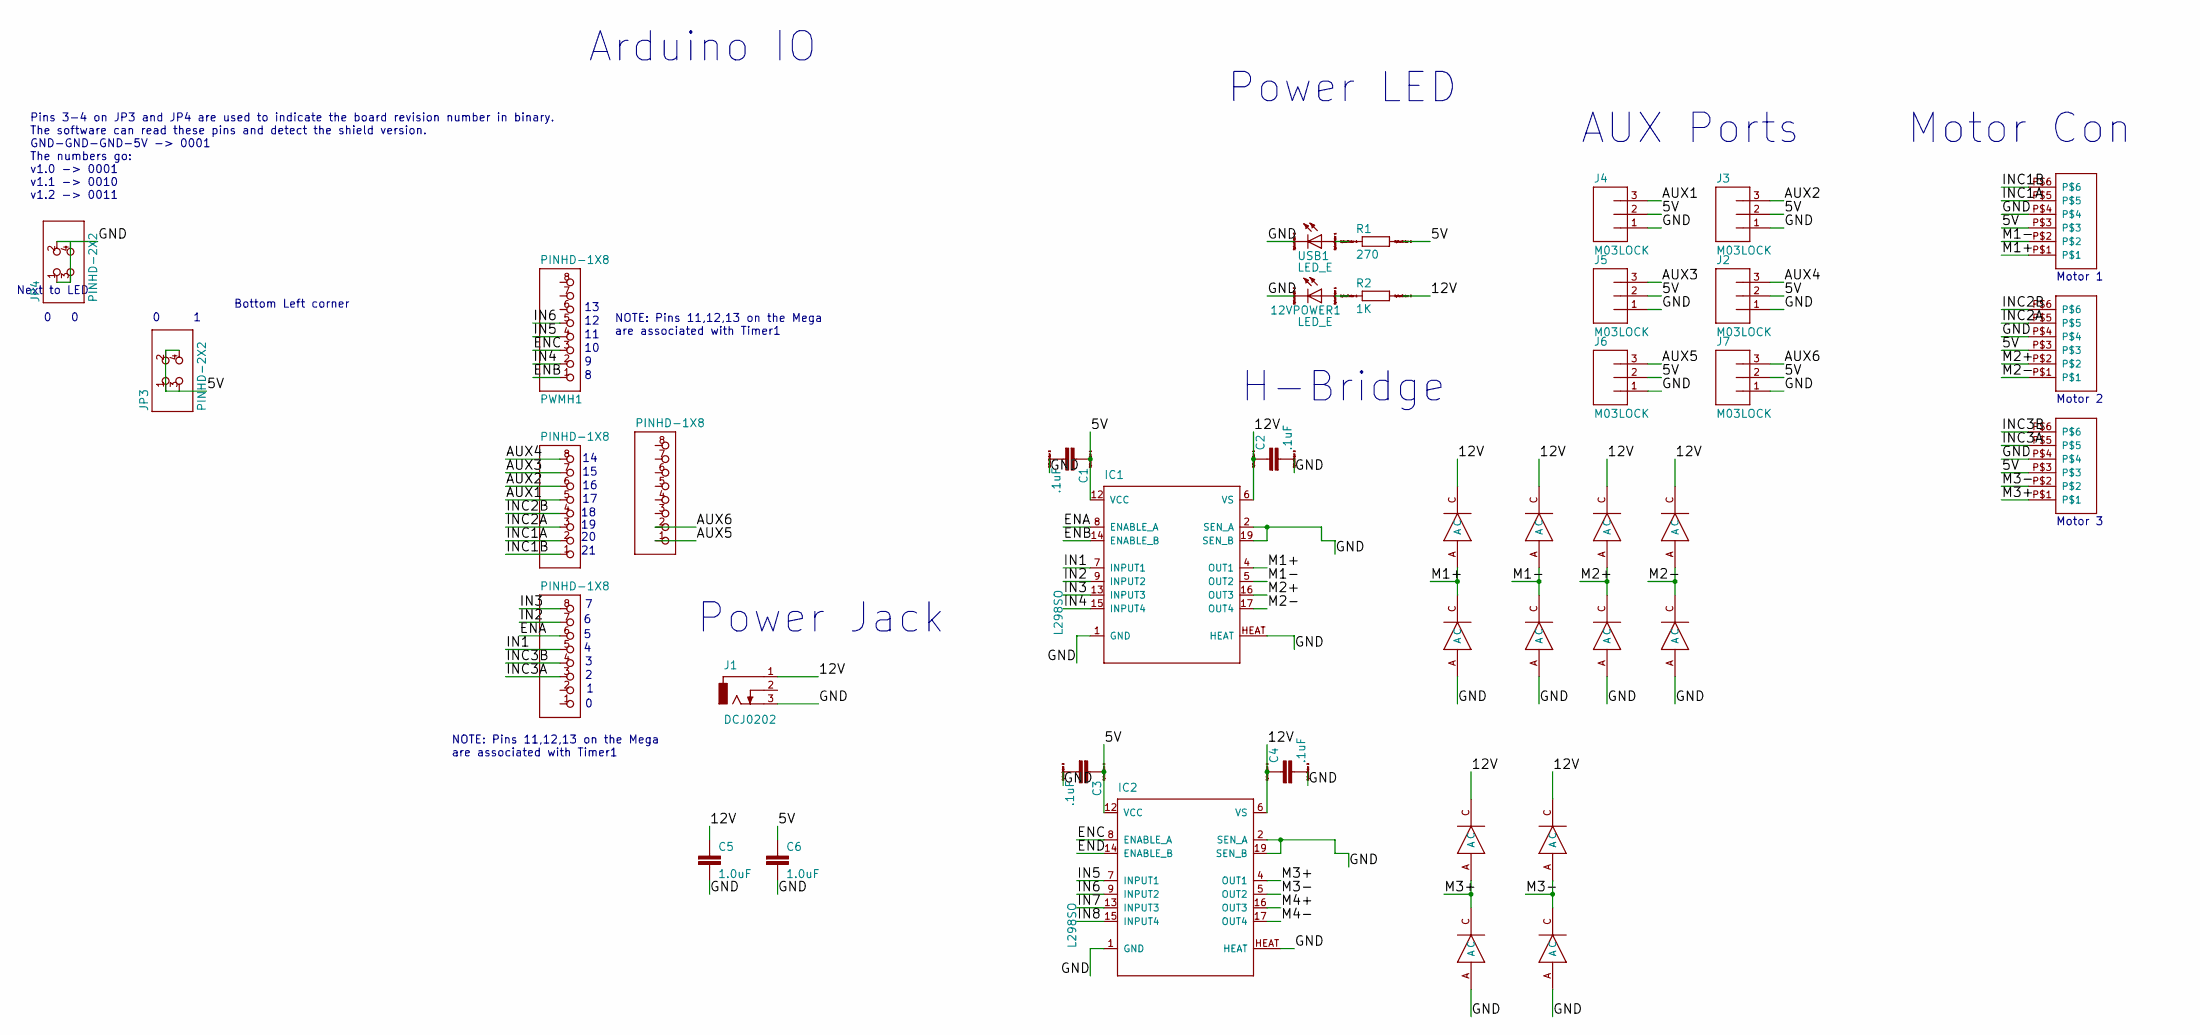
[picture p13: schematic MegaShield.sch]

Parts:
12VPOWER1: LED_E; LED_1206
C1, C2, C3, C4: .1uF; C0805
C5, C6: 1.0uF; 0805-CAP
COMMUNICATION1, COMMUNICATION2: PINHD-1X8; 1X08
IC1, IC2: L298SO; POWERSO-20
J1: DCJ0202
J2, J3, J4, J5, J6, J7: M03LOCK; 1X03_LOCK
JP3, JP4: PINHD-2X2; 2X02
PWMH1: PINHD-1X8; 1X08
PWML1: PINHD-1X8; 1X08
R1: 270; R0805
R2: 1K; R0805
U$1, U$12, U$20: JST-PH-6; JST-PHR-6-SMD
U$2, U$3, U$4, U$5, U$6, U$7, U$8, U$9, U$10, U$11, U$13, U$14: MRA4004; SMA
USB1: LED_E; LED_1206

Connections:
/5V: C1.1, C3.1, C6.1, IC1.12 (VCC), IC2.12 (VCC), J2.2, J3.2, J4.2, J5.2, J6.2, J7.2, JP3.1, JP3.2, JP3.3, JP3.4, R1.2, U$1.P$3, U$12.P$3, U$20.P$3
/12V: C2.1, C4.1, C5.1, IC1.6 (VS), IC2.6 (VS), J1.1, R2.2, U$2.C, U$3.C, U$5.C, U$7.C, U$9.C, U$13.C
/AUX1: COMMUNICATION2.5, J4.3
/AUX2: COMMUNICATION2.6, J3.3
/AUX3: COMMUNICATION2.7, J5.3
/AUX4: COMMUNICATION2.8, J2.3
/AUX5: COMMUNICATION1.1, J6.3
/AUX6: COMMUNICATION1.2, J7.3
/ENA: IC1.8 (ENABLE_A), PWML1.6
/ENB: IC1.14 (ENABLE_B), PWMH1.1
/ENC: IC2.8 (ENABLE_A), PWMH1.3
/END: IC2.14 (ENABLE_B)
/GND: 12VPOWER1.C, C1.2, C2.2, C3.2, C4.2, C5.2, C6.2, IC1.1 (GND), IC1.2 (SEN_A), IC1.19 (SEN_B), IC1.HEAT, IC2.1 (GND), IC2.2 (SEN_A), IC2.19 (SEN_B), IC2.HEAT, J1.3, J2.1, J3.1, J4.1, J5.1, J6.1, J7.1, JP4.1, JP4.2, JP4.3, JP4.4, U$1.P$4, U$4.A, U$6.A, U$8.A, U$10.A, U$11.A, U$12.P$4, U$14.A, U$20.P$4, USB1.C
/IN1: IC1.7 (INPUT1), PWML1.5
/IN2: IC1.9 (INPUT2), PWML1.7
/IN3: IC1.13 (INPUT3), PWML1.8
/IN4: IC1.15 (INPUT4), PWMH1.2
/IN5: IC2.7 (INPUT1), PWMH1.4
/IN6: IC2.9 (INPUT2), PWMH1.5
/IN7: IC2.13 (INPUT3)
/IN8: IC2.15 (INPUT4)
/INC1A: COMMUNICATION2.2, U$1.P$5
/INC1B: COMMUNICATION2.1, U$1.P$6
/INC2A: COMMUNICATION2.3, U$12.P$5
/INC2B: COMMUNICATION2.4, U$12.P$6
/INC3A: PWML1.3, U$20.P$5
/INC3B: PWML1.4, U$20.P$6
/M1+: IC1.4 (OUT1), U$1.P$1, U$3.A, U$4.C
/M1-: IC1.5 (OUT2), U$1.P$2, U$5.A, U$6.C
/M2+: IC1.16 (OUT3), U$7.A, U$8.C, U$12.P$2
/M2-: IC1.17 (OUT4), U$9.A, U$10.C, U$12.P$1
/M3+: IC2.4 (OUT1), U$2.A, U$11.C, U$20.P$1
/M3-: IC2.5 (OUT2), U$13.A, U$14.C, U$20.P$2
/M4+: IC2.16 (OUT3)
/M4-: IC2.17 (OUT4)
unnamed: 12VPOWER1.A, R2.1
unnamed: R1.1, USB1.A

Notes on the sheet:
Motor 1
Motor 2
H-Bridge
Power LED
Power Jack
Arduino IO
AUX Ports
Motor Con
Motor 3
Pins 3-4 on JP3 and JP4 are used to indicate the board revision number in binary. The software can read these pins and detect the shield version. GND-GND-GND-5V -> 0001 The numbers go: v1.0 -> 0001 v1.1 -> 0010 v1.2 -> 0011
NOTE: Pins 11,12,13 on the Mega are associated with Timer1
Next to LED
Bottom Left corner

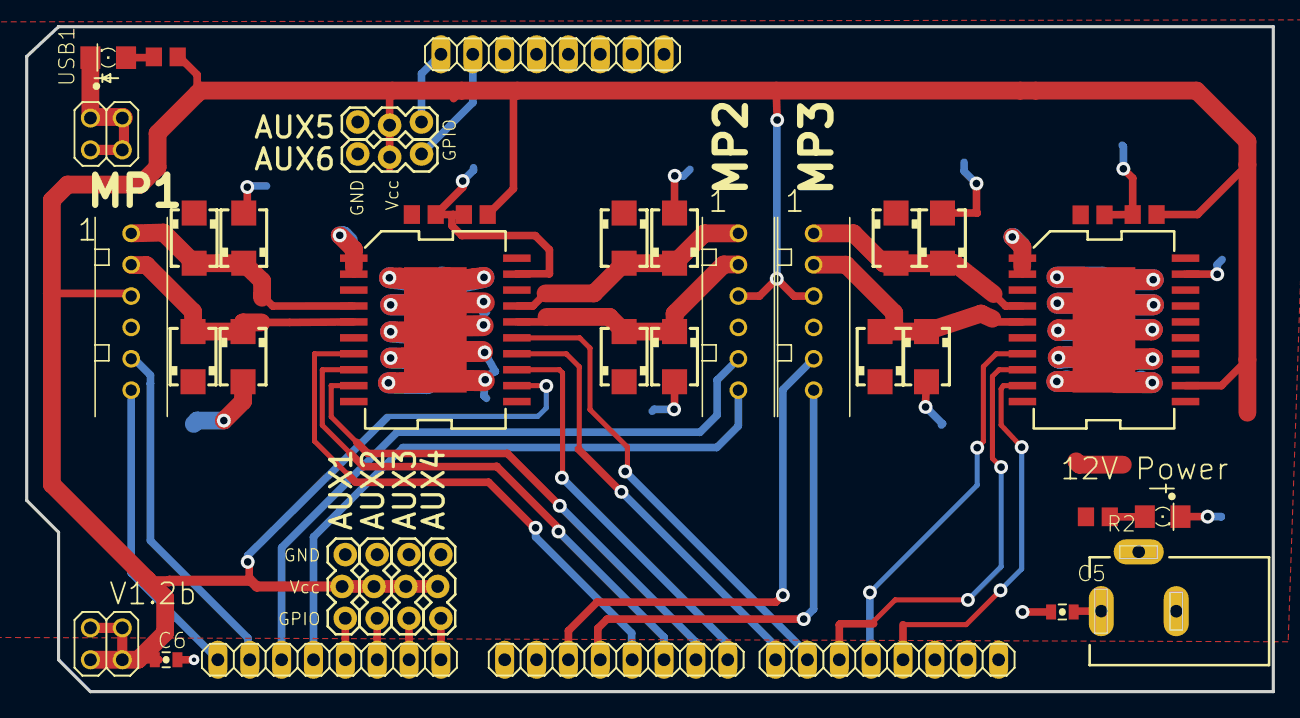
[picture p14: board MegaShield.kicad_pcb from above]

Board: 2 copper layers, 99.4 x 53.0 mm, 40 parts (0 on the bottom side), 32 nets.

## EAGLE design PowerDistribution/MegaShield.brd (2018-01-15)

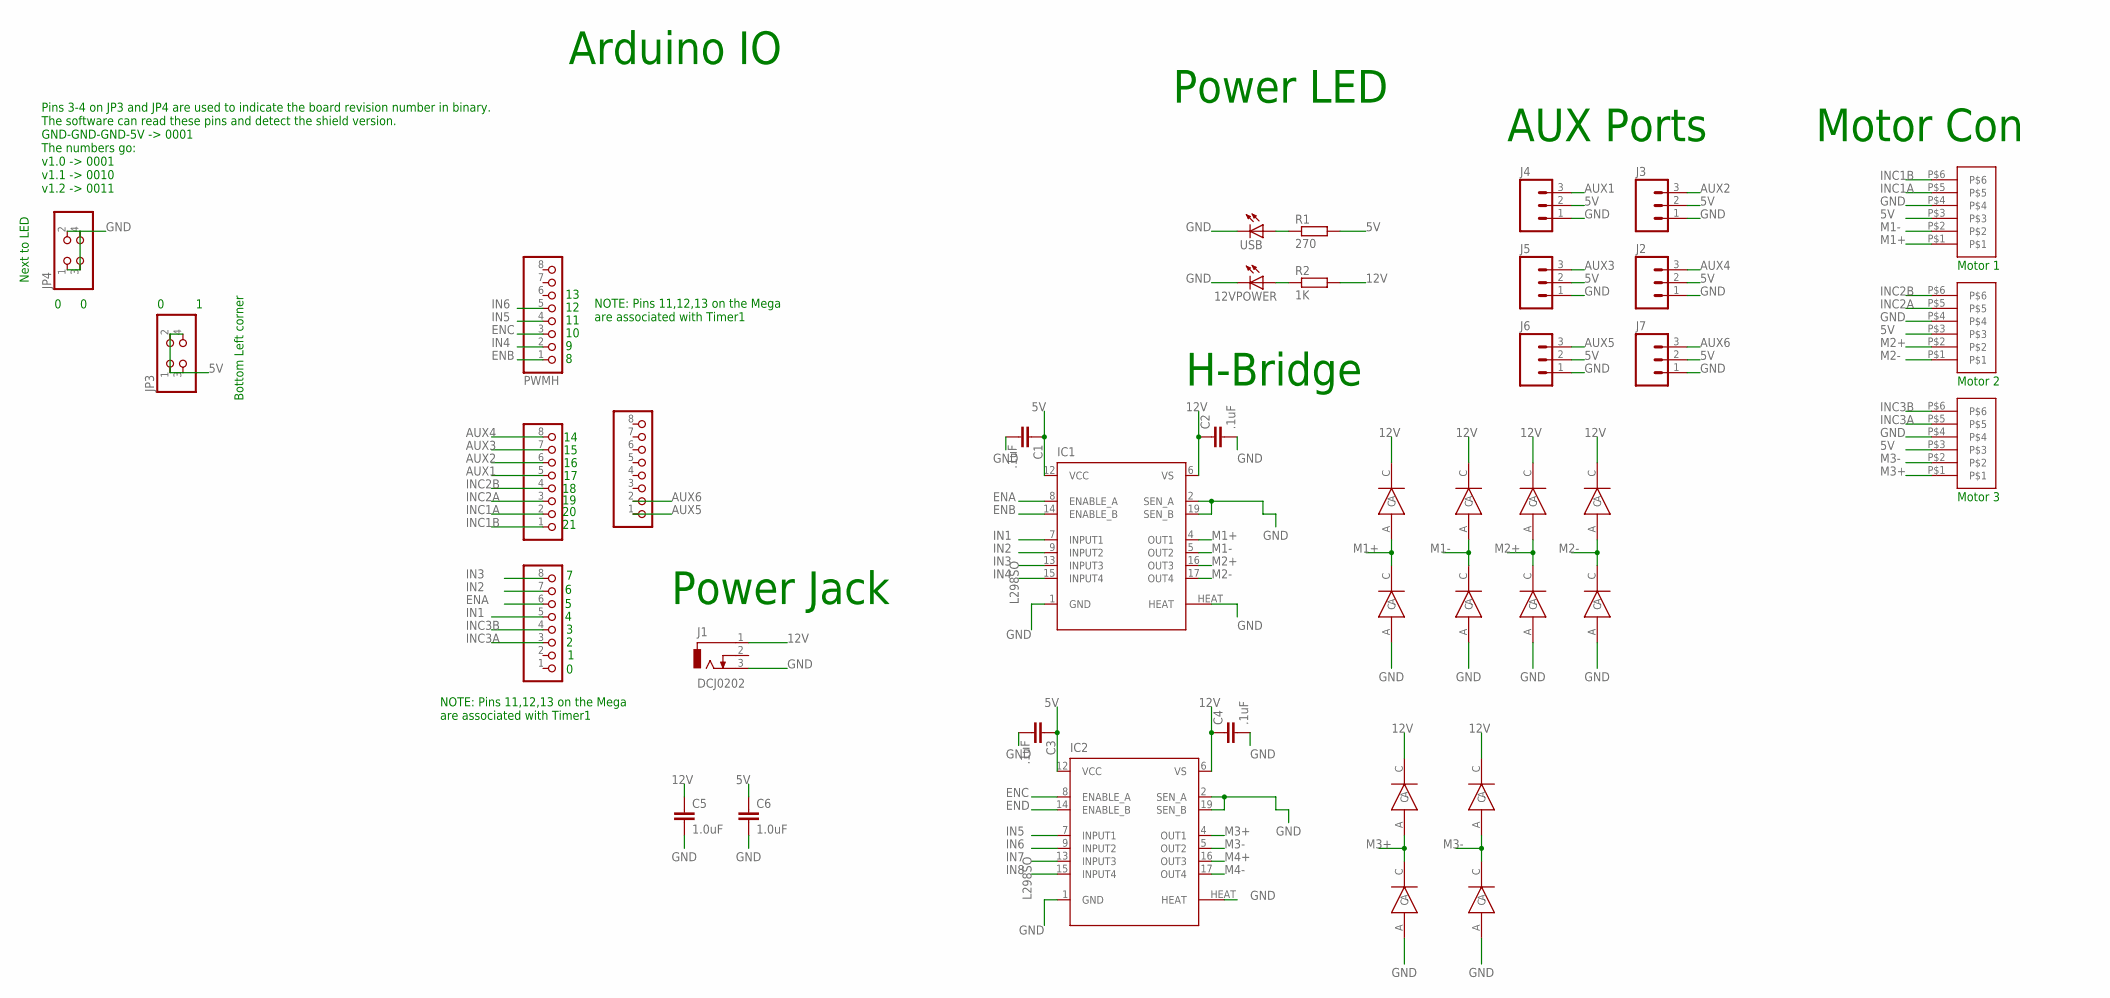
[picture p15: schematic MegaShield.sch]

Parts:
12VPOWER: LED_E; LED_1206
C1, C2, C3, C4: .1uF; C0805
C5, C6: 1.0uF; 0805-CAP
COMMUNICATION, COMMUNICATION1: PINHD-1X8; 1X08
IC1, IC2: L298SO; POWERSO-20
J1: DCJ0202
J2, J3, J4, J5, J6, J7: M03LOCK; 1X03_LOCK
JP3, JP4: PINHD-2X2; 2X02
PWMH: PINHD-1X8; 1X08
PWML: PINHD-1X8; 1X08
R1: 270; R0805
R2: 1K; R0805
U$1, U$12, U$20: JST-PH-6; JST-PHR-6-SMD
U$2, U$3, U$4, U$5, U$6, U$7, U$8, U$9, U$10, U$11, U$13, U$14: MRA4004; SMA
USB: LED_E; LED_1206

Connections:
5V: C1.1, C3.1, C6.1, IC1.12 (VCC), IC2.12 (VCC), J2.2, J3.2, J4.2, J5.2, J6.2, J7.2, JP3.1, JP3.2, JP3.3, JP3.4, R1.2, U$1.P$3, U$12.P$3, U$20.P$3
12V: C2.1, C4.1, C5.1, IC1.6 (VS), IC2.6 (VS), J1.1, R2.2, U$2.C, U$3.C, U$5.C, U$7.C, U$9.C, U$13.C
AUX1: COMMUNICATION.5, J4.3
AUX2: COMMUNICATION.6, J3.3
AUX3: COMMUNICATION.7, J5.3
AUX4: COMMUNICATION.8, J2.3
AUX5: COMMUNICATION1.1, J6.3
AUX6: COMMUNICATION1.2, J7.3
ENA: IC1.8 (ENABLE_A), PWML.6
ENB: IC1.14 (ENABLE_B), PWMH.1
ENC: IC2.8 (ENABLE_A), PWMH.3
END: IC2.14 (ENABLE_B)
GND: 12VPOWER.C, C1.2, C2.2, C3.2, C4.2, C5.2, C6.2, IC1.1 (GND), IC1.2 (SEN_A), IC1.19 (SEN_B), IC1.HEAT, IC2.1 (GND), IC2.2 (SEN_A), IC2.19 (SEN_B), IC2.HEAT, J1.3, J2.1, J3.1, J4.1, J5.1, J6.1, J7.1, JP4.1, JP4.2, JP4.3, JP4.4, U$1.P$4, U$4.A, U$6.A, U$8.A, U$10.A, U$11.A, U$12.P$4, U$14.A, U$20.P$4, USB.C
IN1: IC1.7 (INPUT1), PWML.5
IN2: IC1.9 (INPUT2), PWML.7
IN3: IC1.13 (INPUT3), PWML.8
IN4: IC1.15 (INPUT4), PWMH.2
IN5: IC2.7 (INPUT1), PWMH.4
IN6: IC2.9 (INPUT2), PWMH.5
IN7: IC2.13 (INPUT3)
IN8: IC2.15 (INPUT4)
INC1A: COMMUNICATION.2, U$1.P$5
INC1B: COMMUNICATION.1, U$1.P$6
INC2A: COMMUNICATION.3, U$12.P$5
INC2B: COMMUNICATION.4, U$12.P$6
INC3A: PWML.3, U$20.P$5
INC3B: PWML.4, U$20.P$6
M1+: IC1.4 (OUT1), U$1.P$1, U$3.A, U$4.C
M1-: IC1.5 (OUT2), U$1.P$2, U$5.A, U$6.C
M2+: IC1.16 (OUT3), U$7.A, U$8.C, U$12.P$2
M2-: IC1.17 (OUT4), U$9.A, U$10.C, U$12.P$1
M3+: IC2.4 (OUT1), U$2.A, U$11.C, U$20.P$1
M3-: IC2.5 (OUT2), U$13.A, U$14.C, U$20.P$2
M4+: IC2.16 (OUT3)
M4-: IC2.17 (OUT4)
unnamed: R1.1, USB.A
unnamed: 12VPOWER.A, R2.1

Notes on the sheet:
Motor 1
Motor 2
H-Bridge
Power LED
Power Jack
Arduino IO
AUX Ports
Motor Con
Motor 3
Pins 3-4 on JP3 and JP4 are used to indicate the board revision number in binary. The software can read these pins and detect the shield version. GND-GND-GND-5V -> 0001 The numbers go: v1.0 -> 0001 v1.1 -> 0010 v1.2 -> 0011
NOTE: Pins 11,12,13 on the Mega are associated with Timer1
Next to LED
Bottom Left corner

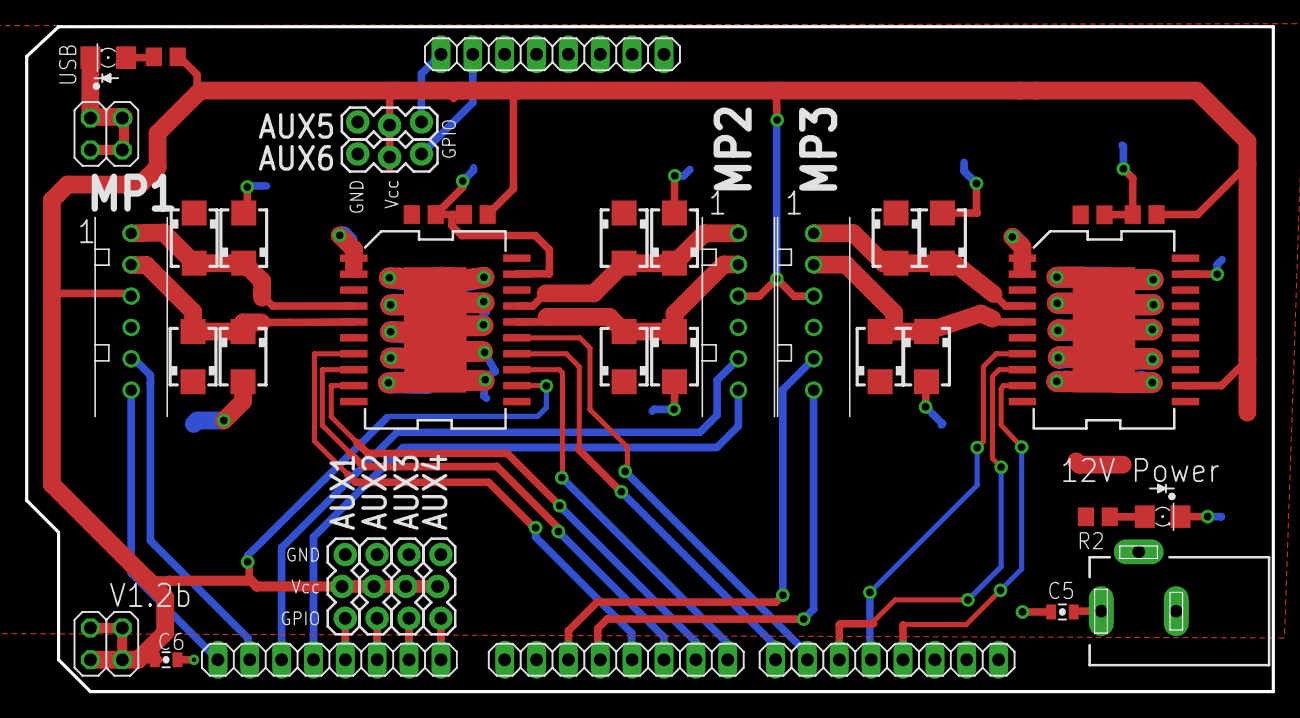
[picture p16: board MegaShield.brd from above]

Board: 2 copper layers, 99.4 x 53.0 mm, 40 parts (0 on the bottom side), 32 nets.

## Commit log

2015-01-29 Added pictures of schematics and layouts
2016-08-19 outline in
    [MegaShield.brd, MegaShield.sch]
2016-08-19 ethernet jacks in
    [MegaShield.brd, MegaShield.sch]
2016-08-20 coming along
    [MegaShield.brd, MegaShield.sch]
2016-08-20 hbridge in
    [MegaShield.brd, MegaShield.sch]
2016-08-20 switch to check LED colors
    [MegaShield.brd, MegaShield.sch]
2016-08-20 shipped here
    [MegaShield.brd, MegaShield.sch]
2016-08-20 commit to switch branches
2016-08-30 started, stopped because not a priority
    [MegaShield.brd, MegaShield.sch]
2016-10-24 revision 2 shipped here
    [MegaShield.brd, MegaShield.sch]
2016-10-24 switched polarity on DC jack
    [MegaShield.brd, MegaShield.sch]
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2016-11-04 cleanup and update pictures
    [AS5048 Encoder.brd, AS5048 Encoder.sch, CNC-CTRL-BRD-Simple.brd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]
2016-11-04 add labels to schematic
    [MegaShield.sch]
2016-11-04 Really added label to schematic
    [MegaShield.sch]
2016-11-04 added schematic to readme
2016-11-15 added aux ports
    [MegaShield.brd, MegaShield.sch]
2016-11-20 smd L298
    [MegaShield.brd, MegaShield.sch]
2016-11-20 before move
    [MegaShield.brd]
2016-11-20 end of night
    [MegaShield.brd]
2016-11-20 2 axis done
    [MegaShield.brd, MegaShield.sch]
2016-11-20 duplicate schematic elements
    [MegaShield.brd, MegaShield.sch]
2016-11-20 parts placed
    [MegaShield.brd, MegaShield.sch]
2016-11-22 routed, not checked
    [MegaShield.brd, MegaShield.sch]
2016-11-22 added aux 5 and aux 6
    [MegaShield.brd, MegaShield.sch]
2016-11-30 put in top header for stability
    [Arduino MEGA blank shield.brd, Arduino MEGA blank shield.sch, MegaShield.brd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]
2016-11-30 add second indicator line to connectors
    [MegaShield.brd, MegaShield.sch]
2016-12-01 started moving things
    [Arduino MEGA blank shield.brd, Arduino MEGA blank shield.sch, MegaShield.brd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]
2016-12-01 shifting and routing
    [MegaShield.brd, MegaShield.sch]
2016-12-01 routed v1
    [MegaShield.brd]
2016-12-08 add missing wire
    [MegaShield.brd, MegaShield.sch]
2016-12-08 change diode placement
    [MegaShield.brd]
2016-12-29 add binary board revision #
    [MegaShield.brd, MegaShield.sch]
2016-12-29 put headers on grid
    [MegaShield.brd]
2016-12-29 add polarity indicator to LED
    [MegaShield.brd, MegaShield.sch]
2016-12-29 diodes all the same direction
    [MegaShield.brd]
2016-12-29 moved up but not re-routed
    [MegaShield.brd]
2016-12-29 much clean up
    [MegaShield.brd, MegaShield.sch]
2016-12-29 wire up 4th axis encoder
    [MegaShield.brd, MegaShield.sch]
2016-12-29 a little more DRC, shipped here
    [MegaShield.brd, MegaShield.sch]
2017-01-12 clean up for PCB production
    [MegaShield.brd]
2017-01-12 maybe something not saved?
    [MegaShield.brd, MegaShield.sch]
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2017-02-04 Tie broken power connection
2017-02-06 swap encoder pins around
    [MegaShield.brd, MegaShield.sch]
2017-02-06 everything lines up
    [MegaShield.brd, MegaShield.sch]
2017-02-06 everything ripped up
    [MegaShield.brd, MegaShield.sch]
2017-02-06 still ripped up, all pins shifted
    [MegaShield.brd, MegaShield.sch]
2017-02-07 looks good except for residual holes under L298s
    [MegaShield.brd, MegaShield.sch]
2017-02-07 builds but not checked yet
    [MegaShield.brd, MegaShield.sch]
2017-02-07 CAM generated
    [MegaShield.GBL, MegaShield.GBO, MegaShield.GBP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]
2017-02-07 move logo
    [MegaShield.GBL, MegaShield.GBO, MegaShield.GBP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]
2017-02-07 redo CAM
    [MegaShield.GBL, MegaShield.GBO, MegaShield.GBP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]
2017-04-01 add motor port numbers and 12v LED
    [MegaShield.brd, MegaShield.sch]
2017-04-02 remove forth axis
    [MegaShield.brd, MegaShield.sch]
2017-04-02 ship here
    [MegaShield.brd]
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2017-07-17 Update documentation pictures and clean up
    [MegaShield.GBL, MegaShield.GBO, MegaShield.GBP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]
2017-08-21 Identify pin1 on connectors MP1, MP2, MP3
    [MegaShield.brd]
2017-09-13 Chip 1 moved over
    [MegaShield.brd, MegaShield.sch]
2017-09-13 more routing done
    [MegaShield.brd, MegaShield.sch]
2017-09-13 All parts routed
    [MegaShield.brd, MegaShield.sch]
2017-09-13 Everything Routed?
    [MegaShield.brd]
2017-09-28 Update board version detection system
    [MegaShield.brd, MegaShield.sch]
2017-09-29 Clean up the pin 2/3 spacing
    [MegaShield.brd]
2017-10-30 Update power connnector on BOM
2017-11-09 fix issue with not recognizing board
    [MegaShield.brd, MegaShield.sch]
2017-11-09 really fix issue with detecting board number and clean up documentation so it won't happen again
    [MegaShield.brd, MegaShield.sch]
2017-11-10 auto save
    [MegaShield.sch]
2017-11-10 Put pin 1 indicator back in the right spot
    [MegaShield.brd]
2017-11-10 Update schematic and board images
2017-12-20 Add datasheet for z-axis motor
    As requested in https://forums.maslowcnc.com/t/z-axis-motor-specs/340/20
2018-01-12 Add Heatsink part number to BOM
    This Mouser part number is slightly shorter, but available in single quantities and costs less than $3:
    Mouser-532-374124B35G
    https://www.mouser.com/productdetail/aavid-thermalloy/374124b00035g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
2018-01-12 Add diode indicators per Issue#22, change net names per Issue#36
    [MegaShield.brd, MegaShield.sch]
2018-01-14 Change value of R2, clean out old version of schematic
    R2 value changed to 1K per Issue #45. Schematic and BOM updated.
    Remove an old .sch file overlooked in previous housecleaning.
    Watch to see that gitignore correctly ignores the '.b#x' and '.s#x' files
    [MegaShield.brd, MegaShield.sch]
2018-01-14 Add caps to 12V and 5V lines
    Board Layout: C5 next to 12V jack J1, C6 next to JP3 bottom left corner.
    Schematic updated
    BOM updated
    Note: branch descended from PR#48, as it uses the schematic and board files from that PR.
    [MegaShield.brd, MegaShield.sch]
2018-03-23 add bom and instructions
2018-03-23 Convert BOM to be markdown
2018-04-14 update attach motors picture to remove labels fro
2021-04-17 feat: Adds initial kitspace files to test
    [1-click-bom.csv]
2021-04-26 Add Gerber Files
    Gerber File exported from Eagle
    [MegaShield_top_bom.csv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]
2021-04-26 Convert Eagle to KiCad
    [MegaShield.kicad_pcb, MegaShield.sch]
2021-05-01 feat: Adds gerbers to kitspace.yml
2021-05-01 fix: Corrects Gerbers folder in kitspace.yml

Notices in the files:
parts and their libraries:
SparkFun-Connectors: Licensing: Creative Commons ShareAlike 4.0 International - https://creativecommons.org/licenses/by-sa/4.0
